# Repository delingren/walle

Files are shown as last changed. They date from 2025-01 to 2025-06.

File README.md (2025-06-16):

# Wall-E 3.0

* QR Code:

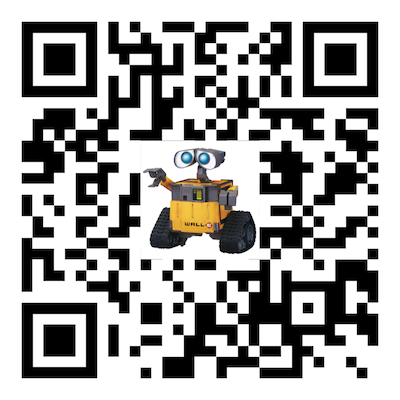
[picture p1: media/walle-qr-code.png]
qr_code
  

* Link: https://github.com/delingren/walle

## Intro

I bought this Wall-E toy made by Thinkway on eBay. Actually I bought a few, all partially broken. The toy is pretty primitive. It can make some basic moves. But the treads cannot be independently controlled. The arms can go up and down a little too, but not independently. The head can turn. The eyes can tilt a little bit. It only has one motor and it's smartly connected to all those parts with a gearbox to make them move in some ways. But in general, there isn't a high degree of maneuverability. It also has a speaker to make some sounds. When new, it came with an IR remote control. None of the units I bought still had it.

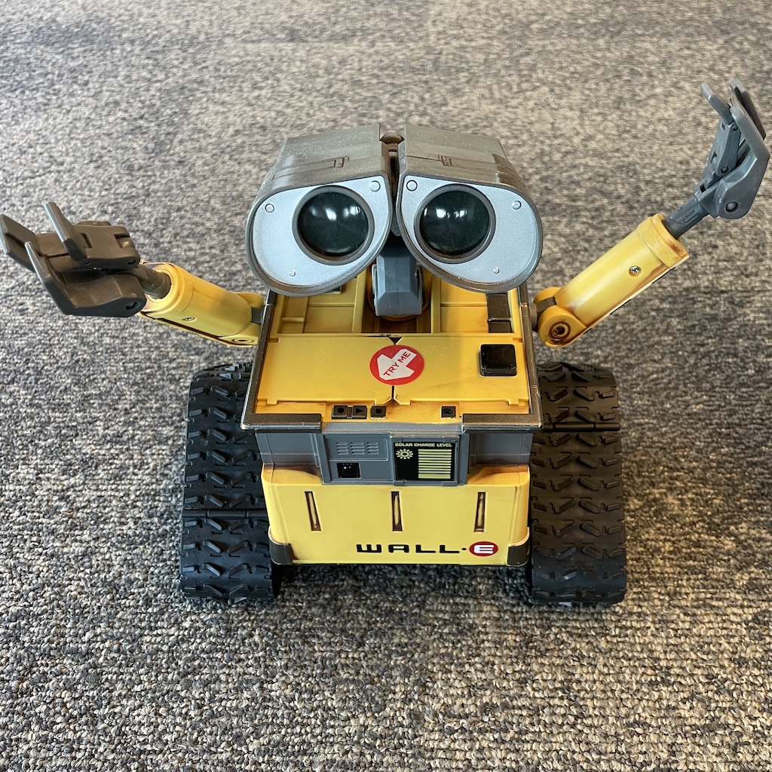
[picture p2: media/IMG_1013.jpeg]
wall-e


My plan is to control it with a microcontroller. The general idea is to gut the internals and replace them with my own parts. The objectives are as follows.

1. Treads can be controlled independently so that they can move forward and backward and at different speeds. This way, the robot can move forward, backward, turn while moving, and spin in place.
1. The arms can lift and lower independently. They only have one degree of freedom. It'd be too complicated to make them do more than that.
1. The head can turn left and right.
1. The eyes can light up. They each have a blue LED inside.
1. The eyebrows can raise and lower, which is done by tilting the eyes around the center.
1. It can play pre-recorded sounds.
1. It can be controlled with remote controls.

The general approach and necessary materials and tools:
1. All the mechanical parts will be 3d printed. I use Fusion 360 for 3d modeling and FlashForge Adventure 3 Lite for printing.
1. The central control unit will be a microcontroller.
1. I will be using Arduino framework to code the mcu.
1. Misc electronic components that will be described in details in this document. All can be found on Amazon or AliExpress.
1. Misc small screws, also found on Amazon or AliExpress.
1. Misc tools such as a soldering station and precision screw drivers and drills.

## Table of Content

The rest of the documentation is organized as follows.

* [Disassembly](disassembly.md)
* Prototyping
  - [Microcontroller](mcu.md)
  - [Controlling arms](arm.md)
  - [Rotating the head](head_rotation.md)
  - [Driving the treads](drivetrain.md)
  - [Driving the eye tilter](eyetilt.md)
  - [Audio](audio.md)
  - [Remote receiver](remote_receiver.md)
* [Remote Control](remote_control.md)
* [RC protocol](remote_protocol.md)
* [Integration](integration.md)
* [Firmware](firmware.md)
* Schematics
  - [Main unit](./schematics/main.svg)
  - [Remote control](./schematics/remote.svg)

* 3D models
  - [Fusion 360 file](./stls/walle_3.0.f3d)
  - [STL files](./stls/)

## Demo

Here is the demo video (on YouTube) of the final product, controlled by a Roku remote control and my custom remote control. It opens on youtube.

demo (https://youtu.be/jzXZmGbrTi8)

## Remote functions

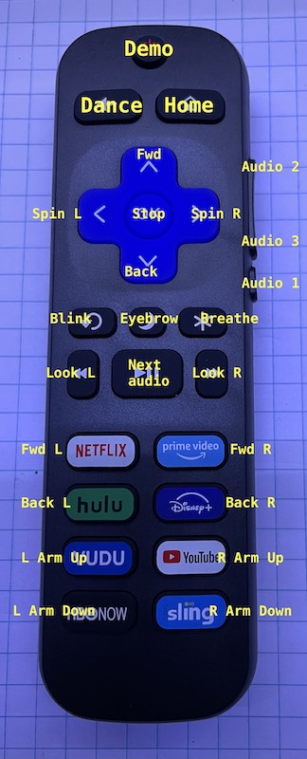
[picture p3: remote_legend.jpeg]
remote_legend


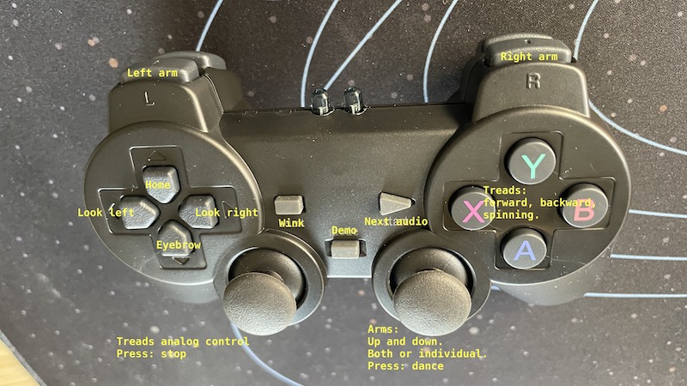
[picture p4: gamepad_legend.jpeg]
gamepad_legend


## Improvement goals over 2.0:
* Use a H-bridge that can provide more voltage hence more torque. In v2, I used an L293D H-bridge IC to drive the DC motors. It turned out it has a pretty high voltage drop. According to the datasheet, the typical motor output voltage is `Vcc - 2.6` and can be as low as `Vcc - 3.6`. I am going to use a MOSFET based H-bridge which would have a much lower voltage drop. I might need to increase the size of the prototype PCB and hence its mount.
* Utilize the "play" mode of the switch. The switch has an off position, and two on positions. One of them is marked as "play" mode. That position connects two additional wires. I can wire one of them to `GND` and another to a GPIO pin, so that I can read from the MCU, thus distinguish the play mode.
* Revise IR remote protocol for better reliability and faster response. In v2, I used a protocol that sends a 32 bit code for each event: button press or joystick coordinate change. The transmission takes 63ms, which means the fastest I can achieve is 15 frames per second. I decided to take a different approach and transmit the state of the gamepad in each frame with 40 bits. The frame rate is still low (actually even lower), but I can transmit the full state of the gamepad in each frame.
* Improve IR remote control for better range. In v2, I drive the IR LED with a GPIO pin, which does not provide enough power. So I'm planning to use a transistor to amplify the signal, and potentially use two LEDs (one wide beam, one normal beam). If the current burst is too much for the batteries to handle and causes the MCU to brown out, we may change the fuses on the Arduino Pro Mini to lower the BOD level.
* Make it possible to change the audio files. In v2, I uploaded the audio files to the audio module's internal flash and soldered it. So it's fixed to UART mode after booting, and the content cannot be 
* Fix the bug where the numbering of the audio files is messed up. Previously, I noticed that the numbering of the audio files did not align with the file names. It turned out that the order has nothing to do with the file names, but is rather dependent on the order of the files in the file system. See [this note](https://github.com/SnijderC/dyplayer?tab=readme-ov-file#important-files-do-not-play-in-order-of-named-sequence). What's the point of naming the files in the specific way then?! I'll try to upload the files individually, from a Windows box.

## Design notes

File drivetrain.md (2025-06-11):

# Driving motors with H-bridges

The main motors need to be able to rotate both directions and the speed needs to be controlled. So we'll use two H-bridges. In v2, I used an IC L293D that has two full H-bridges and can drive 600mA. However, once integrated, I found that the motors were not providing enough torque. I had to reduce the gear ratio and used two 75RPM DC motors. This resulted the tread moving more slowly than I wanted. I did a some trouble shooting and concluded that the two main reasons were the voltage drop on the H-bridge and lack of lubrication in the system. The second was easy to solve with some bike chain lube. For the former one, I decided to look for a different H-bridge IC based on MOSFET instead of BJT. So I came across [this post](https://dronebotworkshop.com/tb6612fng-h-bridge/) that introduces this TB6612FNG breakout board. It uses 6 GPIO pins rather than 4, 3 for each motor. Two pins control the direction and a third one controls the speed via PWM.

So I loaded a [sketch](./debug/motor_hbridge/) to test controlling the speed and direction of two motors. It tries different directions and speeds.

drive_train

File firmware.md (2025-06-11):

# Firmware

There are two independent parts. One for the main toy and one for the remote control. I'm using Arduino framework for both.

## Main

The firmware is relatively straight-forward. One thing worth mentioning is animation. When we receive a command, such as turning the head, we want the operation to be rather smooth. So, instead of setting the position immediately, we animate the transition to the target position. Animation is also needed to create breathing patterns in the eyes. This also applies to the speed of the motors so that they accelerate and decelerate smoothly. So I am defining an `Animatable` class and keep a list of ongoing animations at any moment.

There are at least these two orthogonal aspects to an animation.
1. Absolute value / relative value
1. Transition time / transition speed

So I have defined all these permutations, in addition to a constant animation (or in-animation?). All the transitions are linear. This should be enough for this simple application. Every time we execute `loop()`, i.e. in each frame, we update all the status of all animations.

1. For an ongoing animation, we calculate its transient value by interpolating using the start time, duration, initial value, and target value.
1. If an animation has reached its target value, we remove it from the list and enqueue the next animation.
1. When a new animation is enqueued, we calculate its target value if its value is specified in relative terms.

With the animation library, we can then easily choreograph sequences of moves and associate them with remote control buttons. Since we also have a play mode and a trial mode, we can also do different things based on the mode. I have defined a `trialMode` boolean in the sketch. I'm only using it for the startup moves so far.

### Libraries

Instead of relying on Arduino IDE's library manager, I enlisted DYPlayer and IRRemote libraries as submodules and froze them at the current version. So that it's more self contained and resistant to future breaking changes to these libraries. The Servo library, however, is part of RP2040 board SDK which uses PIO instead of PWM. There is no need to enlist it as a submodule, unless I also enlist the whole SDK, which is unnecessarily complicated.

After enlisting these two libraries, I linked all files in their `src` directories under my sketch's `src` directory. Arduino Framework link all source files under `src` directory. I don't know if there is a way to add a local library. But creating symbolic links is pretty straight-forward with the following bash commands.

```
for i in ../../third_party/Arduino-IRremote/src/* ; do; ln -s $i ; done
for i in ../../third_party/dyplayer/src/* ; do; ln -s $i ; done
```

## Remote Control

The remote control protocol is described in [its own chapter](./remote_protocol.md). The code implementing the sender side simply scans the state of all the controls and sends out a packet. Since the transmission rate is rather low (10 frame per second at most), we don't need to do any debouncing for the buttons. The only interesting bit is scanning the matrix. I'm scanning from column to row. All row pins are pulled up high by default. When we scan, we pull down the column row. If a key at the intersection of the col and row is pressed, it pulls down its row pin. So we can get the state of each button by scanning all the columns and reading all the rows.

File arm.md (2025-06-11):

# Controlling arms

I am going to use servos to control the rotation of the arms and the head. Mechanically, the arms pose a small challenge. I can't disassemble the arm assembly any further without risking damaging the plastic. So I can't get to the axles that the arms rotate around. But I came up with a reasonable solution using the existing mechanism, not requiring the servo shaft and the arm axles to be concentric.

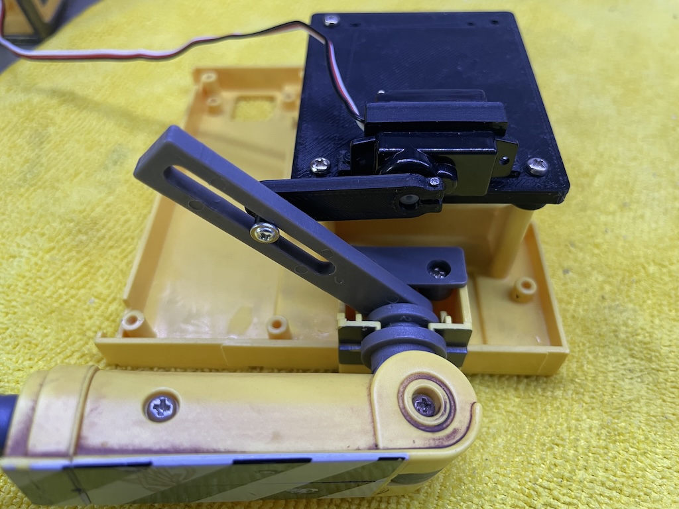
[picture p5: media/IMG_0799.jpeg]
arm_servo


I am using a 5g servo WK-P0050 that I bought from [Amazon](https://www.amazon.com/gp/product/B09TKLQ44L). It's not available there anymore but can be found on AliExpress and other sites.

The servo is fixed on the upper platform with a clamp. The crank is clamped to the servo shaft using an M1 x 5mm screw and a nut. The screw and nut are tiny! The STLs of these parts can be found in the [`stls`](./stls/) folder.

A servo normally rotates 180 degrees. But I don't necessarily need all that range. Its position is controlled with a PWM signal, whose duty cycle width determines the position. Pi Pico's servo library supports specifying the width in microseconds in addition to angles in degrees. So, I am going to map range `[0, 1]` to the minimum and maximum PWM widths, corresponding to the physical range I need for each servo. This way, my code only needs to specify a value between 0 and 1 and the servo will be set to the corresponding position. The details of the servo are abstracted away.

To find out the PWM width ranges, I wrote a [sketch](./debug/servo_calibrate/) which reads a number from the serial console and outputs it to the servo. This way, I can manually enter values to move the servo and find out the minimum and maximum values.

Next, I wrote a [sketch](./debug/servo_sweep/) to sweep the servo back and forth within the range.

sweep

Sweet! Now onto the servo for the head.

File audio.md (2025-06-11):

# Audio

## DFPlayer

I used a [DFPlayer](https://www.dfrobot.com/product-1121.html) in the first version and thought it was a bit expensive (~$20 at the time). But the price has come down quite a bit. AliExpress even has some clones that costs just a little over $1 a piece. It doesn't have internal flash. Instead, it reads from microSD cards. I have quite a few of microSD cards salvaged from all sorts of electronics found in e-waste bins.

So, let's see if it plays nicely with the RP2040-Zero. The board comes with an Arduino [library](https://github.com/DFRobot/DFRobotDFPlayerMini). The wiring is rather simple. You just need to provide it with power and connect it with a UART port, which I'm using `Serial1` on Pi Pico (pins 0 and 1 by default for Tx and Rx respectively), and connect the speaker to the output pins. There isn't much to it. Then I loaded a [sketch](./debug/dfplayer_loop/) to play all 10 audio files on the SD card in a loop. And voila, Wall-E can speak! A couple of caveats to mention:

1. For some reason, reading file count is not very reliable on this board. I think it's this particular board, since I didn't have any issues in the past. No big deal, I just need to hard code it.
1. The board takes 5V DC but I am going to power everything with 4xAA batteries and I hope to get away without using a regulator. It seems to be able to tolerate 6V. But it's safer to put a 1N1007 diode in serial to drop 0.7V.

## DY-SV17F

I also found an even cheaper alternative: DY-SV17F which has 4MB internal flash and a 5W amp. It has some [official documentation](https://github.com/smoluks/DY-SV17F) but no official Arduino library. I found a third party [library](https://github.com/SnijderC/dyplayer) and decided to give it a try with the following [sketch](./debug/dy_sv17f_loop/), similar to the previous one.

It seems to work fine. So I may go with this one for its low cost and simplicity, since it requires no SD card. A few things worth mentioning:

1. The datasheet states that it requires three 10K Ohm resistors to configure it as UART mode. However, in practice, shorting those pins works just fine.
1. It comes with a micro USB port for accessing its filesystem on the flash. It might be an isolated incident but when I copied files from a Mac, the file system was somehow corrupted. I later formatted it and copied the same files from a Windows box and everything was fine.
1. According to the datasheet, the file names need to be in the format of `ddddd.mp3` where `d` is a digit. 
1. Despite conforming to the file name convention, the numbering didn't seem to work in v2. Later I figured out that it actually goes by the order the files are copied, not the names. So I made sure to copy one file at a time and it worked fine.

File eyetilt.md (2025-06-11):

# Driving one-direction motors

The eye tilt is controlled with a single shaft rotating either direction. The shaft is directly connected to an N10 DC motor. There's no need for an H-bridge since we only need one direction. Instead, we need be able to turn it on and off with a MOSFET. We could use a PWM pin to control the speed but that's really unnecessary. We only need one speed.

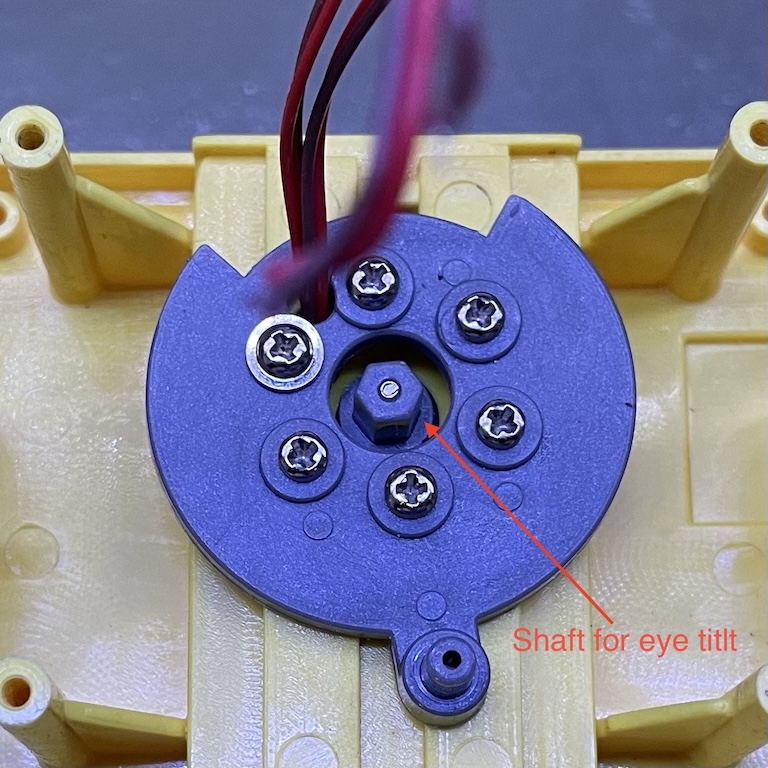
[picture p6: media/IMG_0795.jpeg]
eye tilt shaft


First I connected the motor directly to a 5V power supply and measured about 50 mA of current. So a 2N7000 MOSFET should be good enough to drive it. So I made a quick breadboard prototype and loaded a [sketch](./debug/motor_unidirectional/) to run the motor 3 seconds on and 1 second off repeatedly. It works perfectly.

eye tilt

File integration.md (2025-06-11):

# Integration

## Electronics

I am dividing the electronics into two parts. The lower part is mounted on the chassis near the drive train. It contains the MCU, the audio player, and the H-bridges. The upper part is basically a hub for everything related to the head, arms, IR remote, and the push button. The two parts are connected with a ribbon cable and Dupont connectors.

The power source is first fed to the switch. The switched power is then fed to both the upper and the lower parts. The switch is a three way one. In addition to on and off, there is also a "try me" mode. In that mode, two extra wires are connected. I didn't use it in v2. But here I am connecting one of them to `GND` and the other to a GPIO pin so that we can read the mode. So here's the finished switch, with one input and two outputs. The connectors are 2-pin JST RCYs. The female end can be directly plugged into standard 2.54mm Dupont male connectors. I had to enlarge the existing holes on the switch PCB using a small file. Otherwise it's rather trivial to cut existing wires and solder new ones. The following picture was taken before soldering wires for the mode switch.

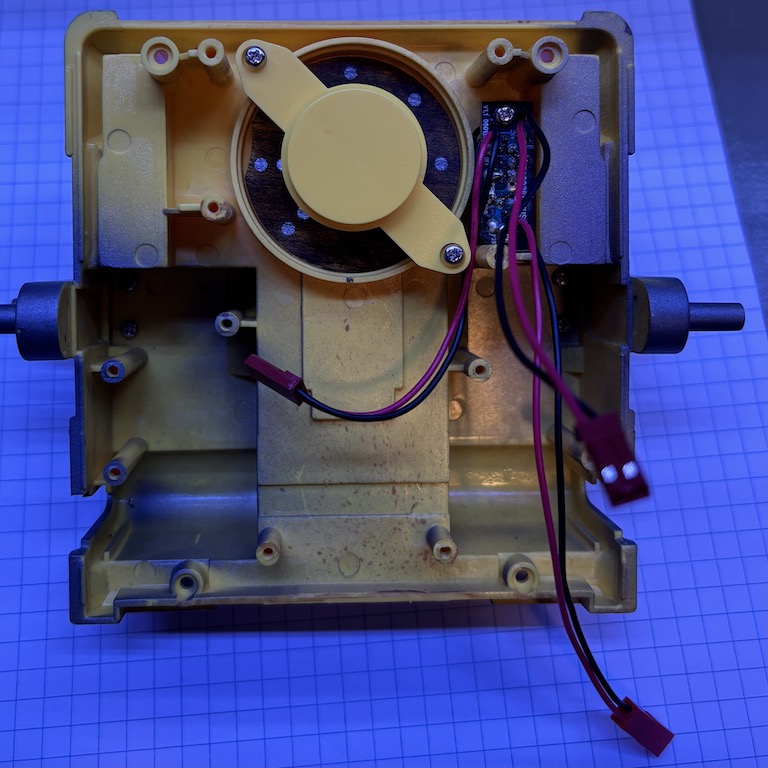
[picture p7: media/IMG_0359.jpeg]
switch


I soldered all electronic components onto a perf board. It has the following interfaces:

* Power source
* Mode switch
* Left and right motors
* Speaker
* Connectors for the upper part

To help with soldering, I first drew all the connections using [Acorn](https://flyingmeat.com/acorn/), a simple image editing tool running on macos, capable of layer editing.

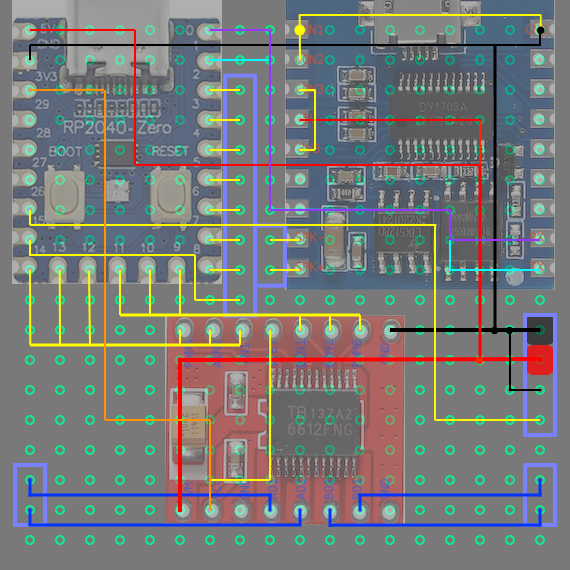
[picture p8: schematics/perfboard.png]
pcb_diagram


Here's the soldered perf board:

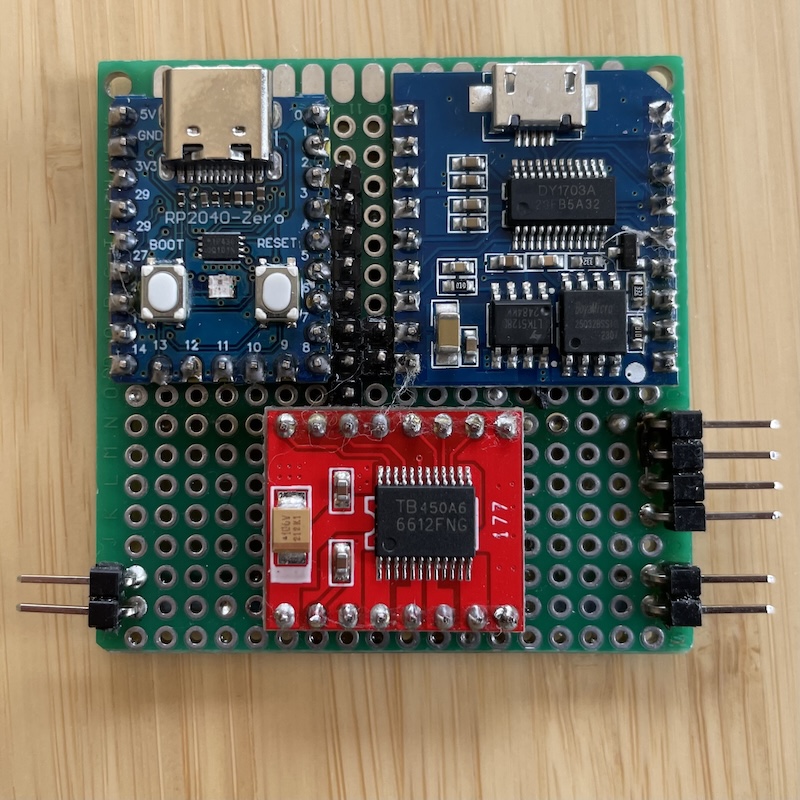
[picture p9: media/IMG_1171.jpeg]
lower_pcb


The PCB is then mounted to the chassis using a 3D printed mount.

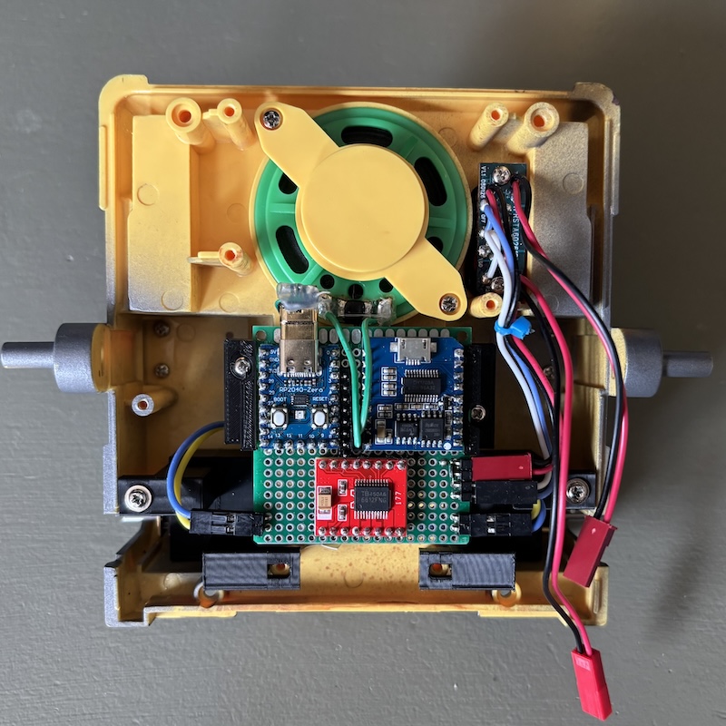
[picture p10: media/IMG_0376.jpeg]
mounted_pcb


Now the upper part. I want to have a neat interface between the upper part and the lower part for easy assembly. So I use a small PCB as a hub and plug everything in the lower part into its pin headers. The PCB has a power bus connected to the switched power source. Then I use a flat ribbon cable to connect all the logic signals. The two IR receivers' signals are combined on the PCB and fed to the MCU via one pin. The MOSFET for the eye tilter motor is also integrated to the PCB. Here are the connections.

1. Eye tilt motor - GPIO 2 
2. IR receiver, front - GPIO 3
3. Eye, right - GPIO 4
4. Eye, left - GPIO 5
5. Head - GPIO 6
6. Arm, left - GPIO 7
7. Arm, right - GPIO 8
8. Push button - GPIO 9
9. IR receiver, back - GPIO 3

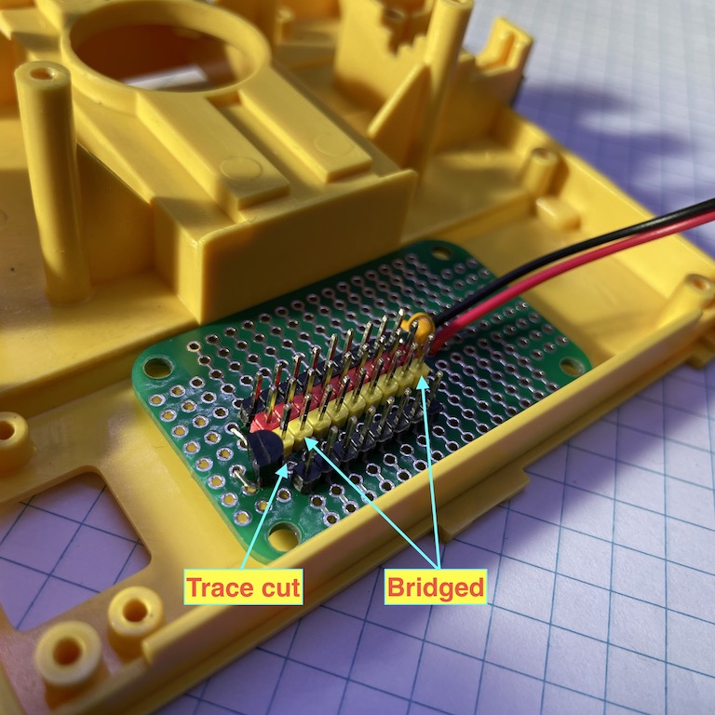
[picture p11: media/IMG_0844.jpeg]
upper_pcb


## Mechanics

For the main drive train, I am mounting the DC motors directly the to driving wheels, using 3d printed parts. The motors are connected to the outputs of the H-bridges. I was originally planning on using a couple of N20 5V 100rpm motors. But it turned out that they don't have enough torque. There is too much friction in the system (let's face it, none of the parts are precisely made and positioned, and there's no lubrication at all). So I ended up using two N30 6V 75rpm versions. They seemed to work fine.

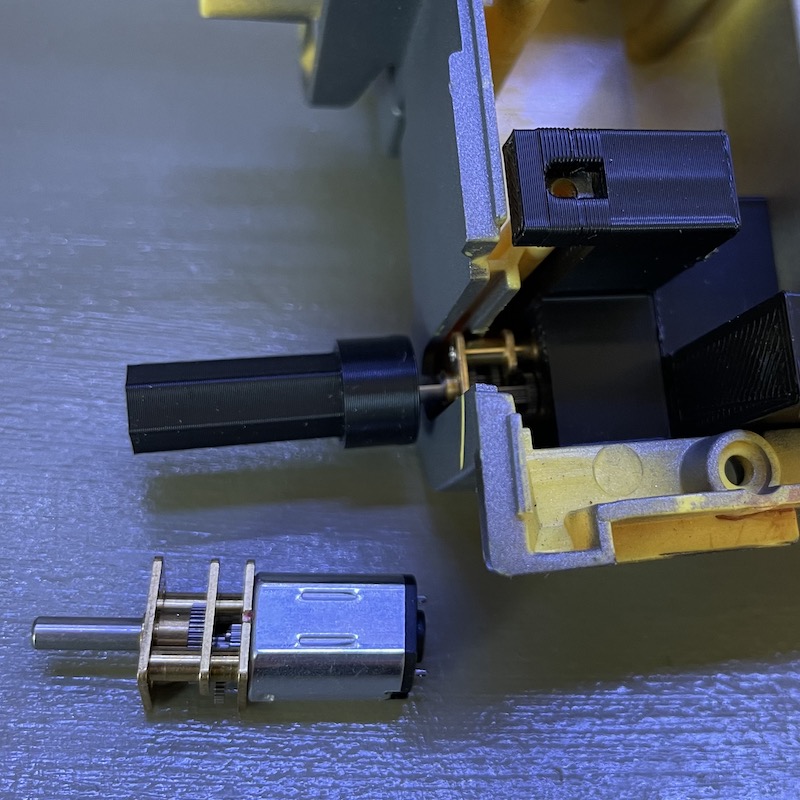
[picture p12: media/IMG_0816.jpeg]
drive_train


For turning the head and tilting the eyes, I already described the mechanism [here](./head_rotation.md) and [here](./motor.md). The servos for driving the arms are described [here](./arm.md). Altogether, I am mounting the three servos and the DC motor on an upper platform.

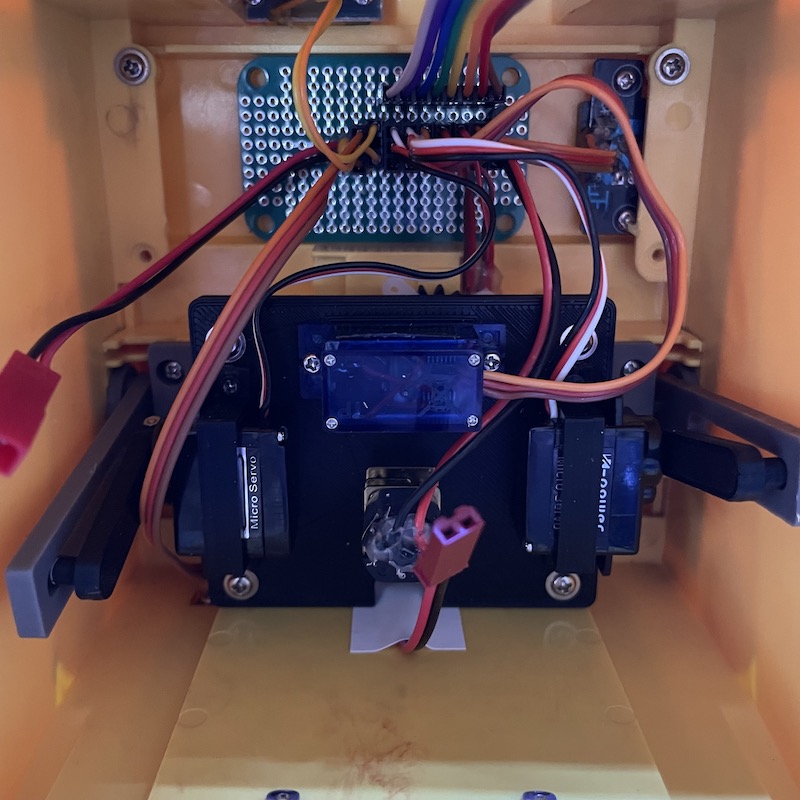
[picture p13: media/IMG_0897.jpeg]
servos


## Calibration and debugging

Before working on the final sketch, I am going through the following steps to make sure all parts are mechanically functioning as expected.

For the upper part:

1. Verify eye LEDs
1. Verify IR remote receiver
1. Verify eye tilter motor
1. Verify push button
1. Verify arm and head servos
1. Calibrate servos to determine their limits

upper

For the lower part:

1. Verify both DC motors can turn both directions and the speed can be controlled with PWM pins

lower

Before closing everything up, I am also exposing a USB-C port for uploading sketches and debugging through the serial port. To do this, I cut a hole at the bottom of the chassis, and mounted a panel-mount USB-C port (bought from AliExpress). Then soldered a male USB-C plug on it. Note that I am not connecting the V+ wire, to avoid accidental current backflow to the computer. So it needs to be powered by the batteries when uploading the sketch.

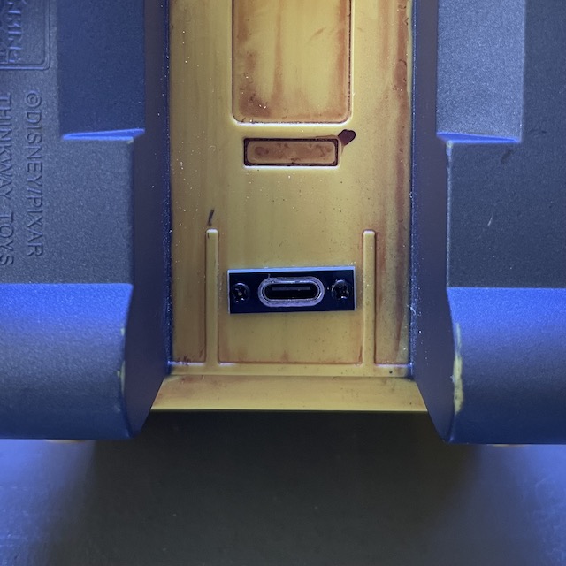
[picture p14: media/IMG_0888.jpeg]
bottom_usb


Now all the mechanical parts are in place and properly assembled. It's time to play with the firmware.

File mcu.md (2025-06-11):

# Microcontroller

We need to choose a microcontroller. I am not going to make a custom PCB for this project. Instead, I will use a dev board and a perf board. There are a few factors to consider.

1. There needs to be enough pins.
1. Dimension. We want the board to be compact.
1. Power. Ideally, I want to be able to power the board with 4 AA batteries, so that I don't need an extra 5V DC regulator.

Here's a tally of the minimum pin needs. These pins will be explained in detail in later sections.

* PWM output: 7 pins
  - Left tread H bridge (1)
  - Right tread H bridge (1)
  - Left eye LED
  - Right eye LED
  - Eye tilt motor

* Digital output: 4 pins
  - Left tread H bridge (2)
  - Right tread H bridge (2)

* Servos: 3 pins. Generally, libraries use PWM to control servos. Some may use PIO on Pi Pico.
  - Left arm servo
  - Right arm servo
  - Head servo

* Input: 2 pins
  - IR sensor
  - Push button

* UART for audio: 2 pins. Note that not all pins can be used for UART.
  - Rx
  - Tx

I have a few [RP2040-Zero dev boards](https://www.waveshare.com/rp2040-zero.htm) in my drawer. They are compatible with Raspberry Pi Pico but has a much smaller footprint.

* Dimensions: 18 x 23.5
* Regulator: ME6217 (LDO, 800mA, max input 6.5V)
* GPIOs: 20 via the header, all capable of PWM.
* UART: 2; UART0 defaults to GPIO0(Tx) and GPIO1(Rx).

It seems to fit the bill really well. So I'll be using it during the prototyping phase and see if it works for everything.

First off, let's verify that all the GPIO pins are PWM capable by using a simple [sketch](./debug/pwm/) to dim LEDs. Sure enough, all these 20 pins are able to fade the LED. This takes care of the eyes. These pins should be good for controlling motors and servos as well. But let's verify on a breadboard in a minute.

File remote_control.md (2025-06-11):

# Custom Remote Control

In addition to using an existing remote control, I also wanted to make my own remote control with joysticks. The biggest challenge is probably 3d printing the housing. So I am exploring the option of using an existing wireless PS2 control bought on AliExpress, gutting the inside and replacing it with a microcontroller and adding an IR LED.

To do that, there are a few things I need to figure out.

1. The joysticks. A PS2 controller has two of them. They are both 2-axis joysticks. I assume they are resistive (i.e. potentiometers) and I should be able to use an ADC pin to read the position of an axis.
1. The IR emitter. This should be relatively easy. The library I use on the receiver side is also capable of sending.
1. The microcontroller. The PS2 controller is powered by 2 AAA batteries, I want to be able to reuse the power source. So I need an mcu that can be powered at 3V. First thing that came to my mind is ATmega 328. I have a couple of them and they are 8MHz versions.

## Microcontroller
As mentioned before, I intend to use an 8MHz ATmega328 dev board (Arduino Pro Mini clone), which should be able to run at 3V comfortably. So I am going to prototype everything on that board. One small caveat about working with this board is that ATmega328 comes in two versions: 8Mhz and 16MHz. When programming with Arduino IDE or CLI, we need to choose the correct frequency. Otherwise, the code will still run, but the timing is all messed up. Anything that relies on the frequency will not work properly. E.g. the serial console or the IR transmitter.

## Range
In v2, one issue I encountered was that the range of the remote control was poor. It turned out that these IR LEDs are designed to endure very high peak current, up to a few hundred mA, which GPIO pins cannot provide. So in v3, I am using a BJT to amplify the signal. In addition, I am putting two LEDs in series, one regular (TSAL6200) and one wide beam version (TSAL6400).

To test the range, I devised an easy tester. On the [sender side](./debug/irrange_sender/), I repeatedly send the same code. On the [receiver side](./debug/irrange_receiver/), I check and verify the code repeatedly. If the code is not received within a timeframe, I light up a red LED. If the code is incorrect, I light up a yellow LED. Then I can walk around the room and test how far I can walk from the receiver and it still remains green.

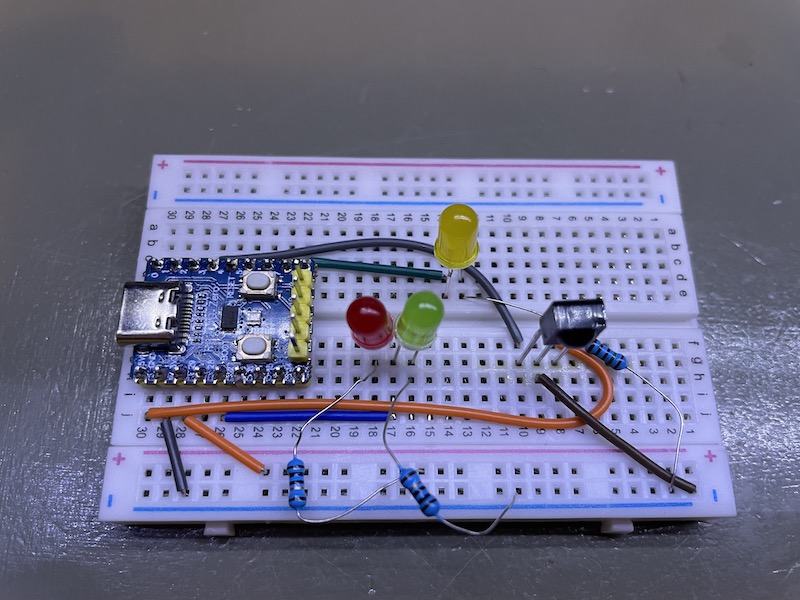
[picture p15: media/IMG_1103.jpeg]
range_tester


It turned out that with two LEDs in series, I can reach a range of at least 6-7 meters on my testing apparatus. In practice, since the IR receiver is behind a brown window, the reception is weakened and partially blocked. But it still works well within 3-4 meters. Not too bad.

### Power saving
The MCU itself can be powered by 1.8-5.5V DC. And since I'm using batteries, I don't need the regulator. Removing it will increase the battery life and eliminate the voltage drop. I connect the battery power directly to the `Vcc` pin. While I'm at it, I also removed the power indicator, the built-in LED, their resistors, and the reset button.

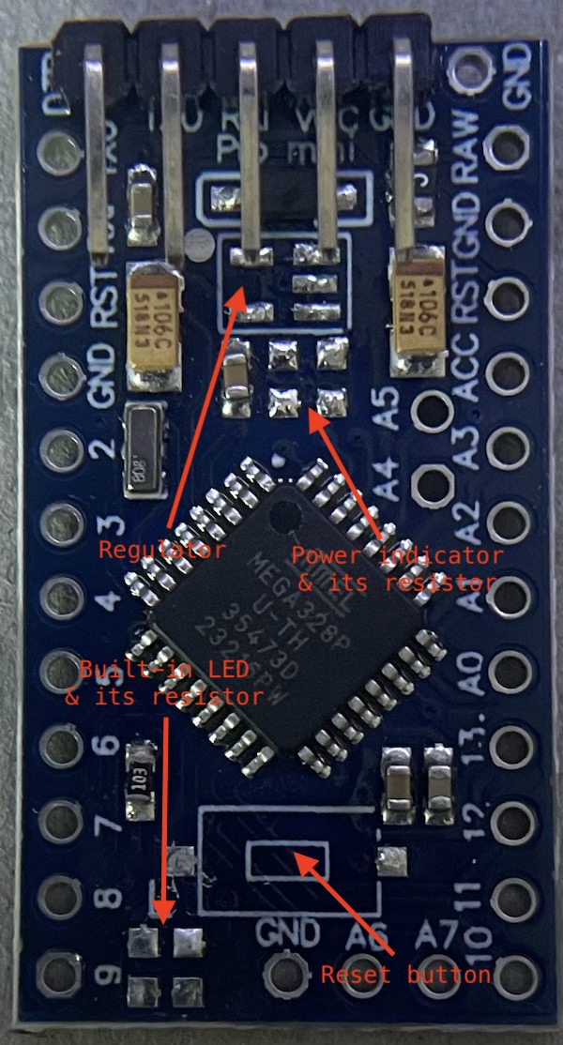
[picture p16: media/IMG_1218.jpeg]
arduino pro mini


## Controller Wiring
I got a couple of different wireless gamepad controllers from AliExpress and disassembled them. They both have tow major PCBs. PCB1, the main PCB, contains the battery box, the IC and various buttons. PCB2 contains two joysticks and a switch. Long story short, this particular one's main PCB has everything I need and needs minimum modification. However, it turned out its joysticks are digital, not analog. On the other hand, the other controller's joysticks are analog and the PCB has the same dimensions. So I created a Frankenstein controller from both of them. In the end, it worked fine. But it was a lot of soldering of thin wires under a magnifier and it was hard on the eye. Next time, I'll probably design a custom PCB and just reuse the shell.

PCB1 contains:
* Left thumb: `L`, `R`, `U`, `D`
* Right thumb: `A`, `B`, `X`, `Y`
* Left index finger: `L1` & `L2`
* Right index finger: `R1` & `R2`
* Middle section: `Select`, `Mode`, `Start`
* A main IC, a transmission IC, and some passive components

I have no use for the components except the two LEDs and their resistors. So let's heat up the PCB with a heat gun and remove them. I suspected all those buttons would be connected to the main IC in some way, forming a matrix. So I traced the PCB traces and determined the following connections.

| | col 1 | col 2 | col 3 | col 4 | col 5 | col 6 | col 7 | col 8 |
|---|---|---|---|---|---|---|---|---|
| **row 1** |  `R1` |  `R2` |  `L1` |  `L2` | `SEL` |`MODE` | |`START`|
| **row 2** |  `A`  |  `X`  |  `B`  |  `Y`  |  `D`  |  `U`  |  `R`  |  `L`  |

Then I marked the pads on the PCB. If two pads are connected with a trace, I use the same label. My hope is not have to cut any traces, which seems feasible here. The only small caveat is that the LEDs' resistors are somehow connected to pads 15 and 16, which is also columns 7 and 8. I don't know why and how it's multiplexed. So I de-soldered the resistors, taped the pads over using a piece of Kapton tape and put the resistors back in place with one pad soldered. Then I added a wire to connect the resistors it to pad 17 and `GND`. I plan to connect `LED1` it to `GPIO13`, the built-in LED pin, and remove the built-in LED on the dev board. I am going to light it up when sending signals. The other LED is the power indicator. Its anode is connected to `BAT+`. So I just connected its resistor to `GND` so that when `GND` is connected to the `BAT-` by the switch, the LED will light up.

And the pins for the rows and columns for the button matrix and the GPIO pin I intend to use:  
```
row 1: pad 06  (GPIO11)
row 2: pad 07  (GPIO12)
col 1: pad 04  (GPIO02)
col 2: pad 09  (GPIO03)
col 3: pad 10  (GPIO04)
col 4: pad 11  (GPIO05)
col 5: pad 13  (GPIO06)
col 6: pad 14  (GPIO07)
col 7: pad 15  (GPIO08)
col 8: pad 16  (GPIO09)
```

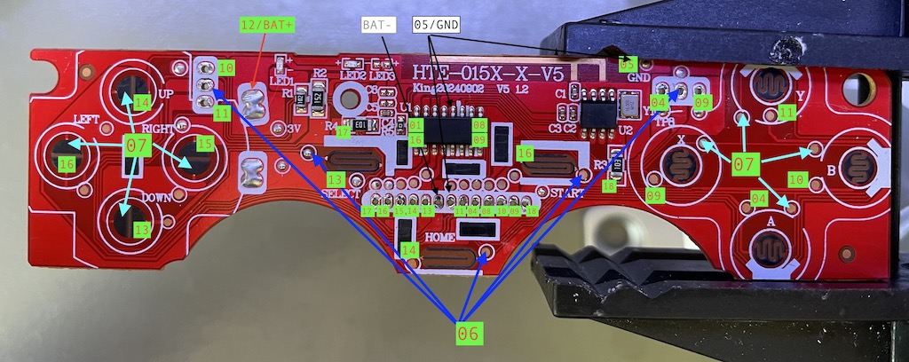
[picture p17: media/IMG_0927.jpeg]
pcb1


We will need these outgoing wires: 
* to PCB2: `BAT-`, `GND`
* to MCU: `BAT+`, `GND`, `Rows 1-2`, `Cols 1-8`, `LED1`

I shorted pads 7 and 8, pads 18 and 6, pad 17 and LED1. This way, all connections except `BAT+` can be made from the pads with holes in the middle.

PCB2 contains:
* Joystick 1, with axes `X1`, `Y1`, and button `J1`
* Joystick 2, with axes `X2`, `Y2`, and button `J2`
* A sliding switch `SW`

When turned on, the switch shorts `BAT-` to `GND`. The two buttons short their pins to `GND` when pressed. The joysticks are analog. Each axis is a potentiometer. It has a high and a low inputs. The output is the wiper. I'll short the low to `GND` and connect the high to  `GPIO A5`. I can then pull the pin high and read the wiper pins as analog pins to determine the position of the axis.

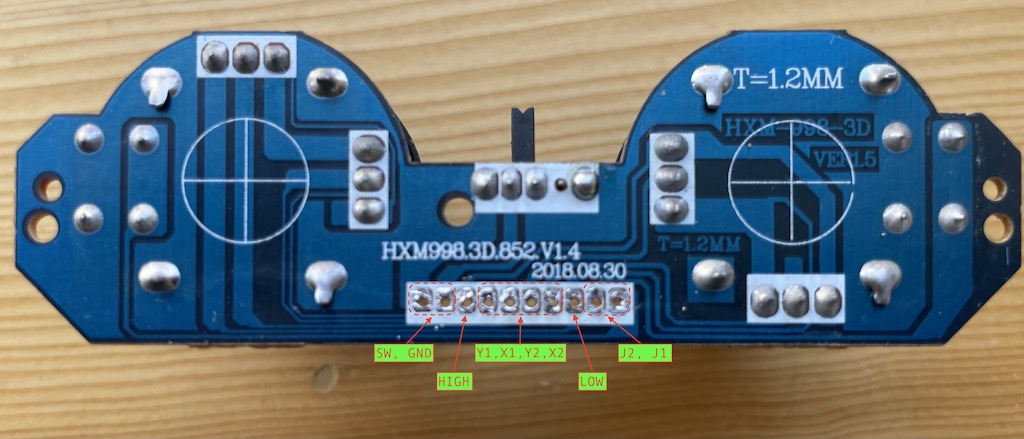
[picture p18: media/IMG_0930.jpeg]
pcb2


Here's the plan for connections:
* Short `LOW` with `GND`
* Connect `SW` to `BAT-` from PCB1
* Connect `GND` to `GND` from PCB1, which ultimately connects to `GND` of the MCU

This way, when the switch is turned on, `BAT-` is connected to `GND` of both PCBs and the MCU. 

Outgoing wires:
* to PCB1: `BAT-`, `GND`
* to MCU: `HIGH`, `X1`, `Y1`, `X2`, `Y2`, `J1`, `J2`

For the analog joysticks, we feed a high to `HIGH`, and read the positions from `X1`, `Y1`, `X2`, `Y2`. I could connect `HIGH` to `Vcc`. But I want to pull it high only when I'm reading the values. This will save a little battery, at the cost of using an extra pin. Now to tally all the GPIO pin usage, we need to use 17 input pins, 4 of which need to be able to analog. Note that `A6` and `A7` are analog input only for Pro Mini. So I'll use them for a joystick. Pin `13` is the built-in LED. I could remove the LED and reclaim the pin. But I might find a use for it later. So I'm saving pin `13`. We also need one digital output pin to drive the IR LED. That's 18 GPIO pins in total. The dev board I have, basically a clone of Arduino Pro Mini, has just enough.

PCB1 ↔ MCU:
* `BAT+` ↔ `Vcc`
* `GND` ↔ `GND`
* `Rows 1-2` ↔ `11`, `12`
* `Cols 1-8` ↔ `2` - `9`

PCB2 ↔ MCU:
* `HIGH`: `A5`
* `X1`, `Y1`, `X2`, `Y2` ↔ `A2`, `A3`, `A6`, `A7`
* `J1`, `J2` ↔ `A0`, `A1`

And,
* IR LED: `10`.

After some soldering and hot gluing, here are the PCBs and the dev board all connected.
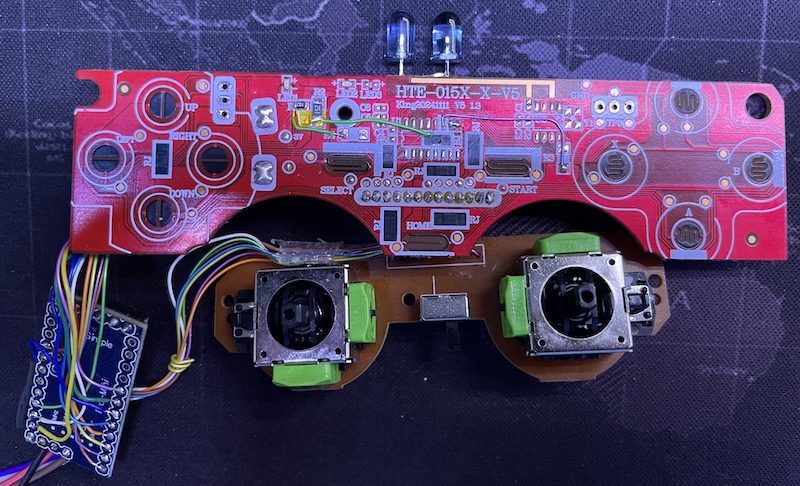
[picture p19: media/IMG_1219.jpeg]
soldered


And after some drilling and cutting, I've placed the IR LED on the shell, with the resistor soldered to it and `BAT+`.
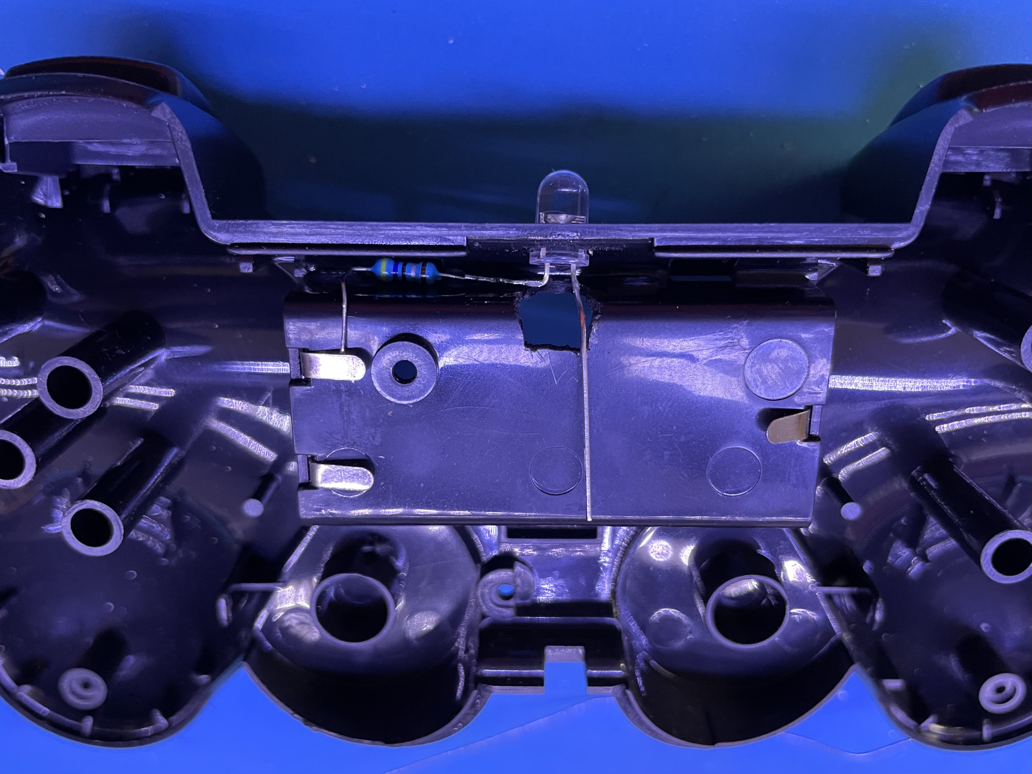
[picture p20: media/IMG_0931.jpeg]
shell


And voila! We have a custom remote control.

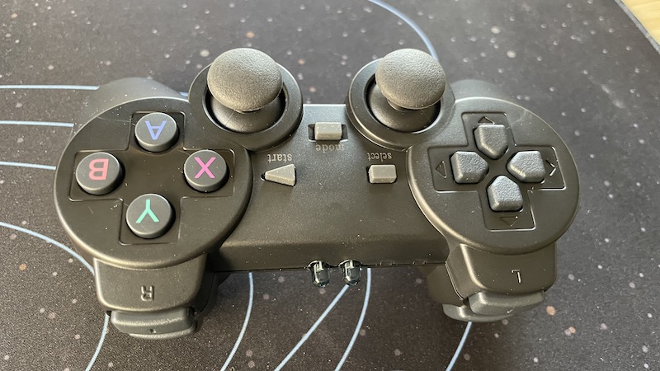
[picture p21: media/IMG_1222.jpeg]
finished


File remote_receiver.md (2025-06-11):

# IR Remote Receiver

The original toy came with a remote control but none of mine had it when I bought them. Not that I really want to use it. Instead, I want to be able to use an existing remote control. In addition, I want to make my own. Wall-E has two IR sensors, one on the shoulder and one on the back. I can either reuse them if they work or replace them with my own if needed.

First order of business is to verify that the sensors responds to my remote control. I have collected some remote controls from e-waste bins in the past. It's time to put them to good use. You probably have figured out by now that dumpster diving is one of my hobbies. Different manufacturers have different IR remote protocols. Many are either publicly available or has been reverse engineered. Here's a very [comprehensive tutorial](https://dronebotworkshop.com/ir-remotes) on this topic. To decode the signals, I am going to use this [Arduino-IRremote library](https://github.com/Arduino-IRremote/Arduino-IRremote). There are some other libraries available for Arduino.

First, I wired up a receiver and checked the waveform with an oscilloscope.

oscilloscope

Next, I loaded a simple [sketch](./debug/irreceiver_print/) to print out the raw data. I'm getting something like this on the serial console:

```
Protocol: 10 Raw code: 3759747205
Protocol: 10 Raw Code: 0
```

The particular remote I want to use is a Roku remote. It seems to use NEC and NEC2 protocols. All repeats are NEC2 and all initial presses are NEC. I don't need or want repeats. So I'll just decode NEC (8). Here's the list of the codes for all the buttons, which will be used in the decoding logic.

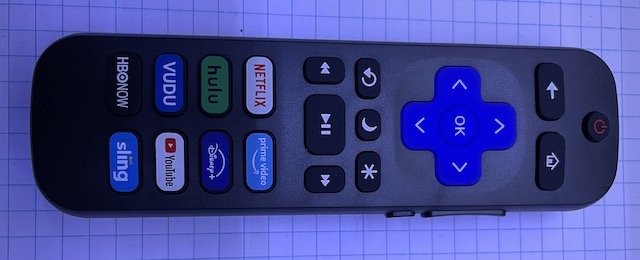
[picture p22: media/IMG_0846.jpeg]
remote


* Power: 3893872618
* Back: 2573649898
* Home: 4228106218
* Up: 3860449258
* Left: 3776890858
* OK: 3576350698
* Right: 3526215658
* Down: 3425945578
* Repeat: 2272839658
* Sleep: 2640496618
* Star: 2657208298
* Rewind: 3409233898
* Pause: 3008153578
* F. Fwd: 2857748458
* Netflix: 2907883498
* Amazon: 3024865258
* Hulu: 2991441898
* Disney: 4077701098
* Vudu: 4144547818
* YouTube: 2841036778
* HBO: 2974730218
* Sling: 4177971178
* Vol Up: 4027566058
* Vol Down: 4010854378
* Mute: 3743467498

A couple of notes:
* It looks like the receivers have no problem with 6V DC. So I am going to connect them directly to the power source.
* Putting two receivers in parallel doesn't seem to cause any problems. So that's what I am going to do.

I also want to be able to make my own joystick IR remote control. To do that, I can either devise my own protocol, since I have full control on both sides, or piggyback on an existing one, as long as it's capable of encoding all the info I need. The IR library I use is capable of both decoding and encoding.

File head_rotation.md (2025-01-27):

# Rotating the head

Since the head assembly is heavy, I am going to use a stronger 9g servo SG90, a staple servo that comes with any Arduino kit. I am replacing the original plate with a 3d printed gear with mounting holes matching the original holes on the plate. The original plate also has an opening whose either end would hit a limiter when the maximum range is hit. So I have removed some teeth from a full gear to achieve the same function.

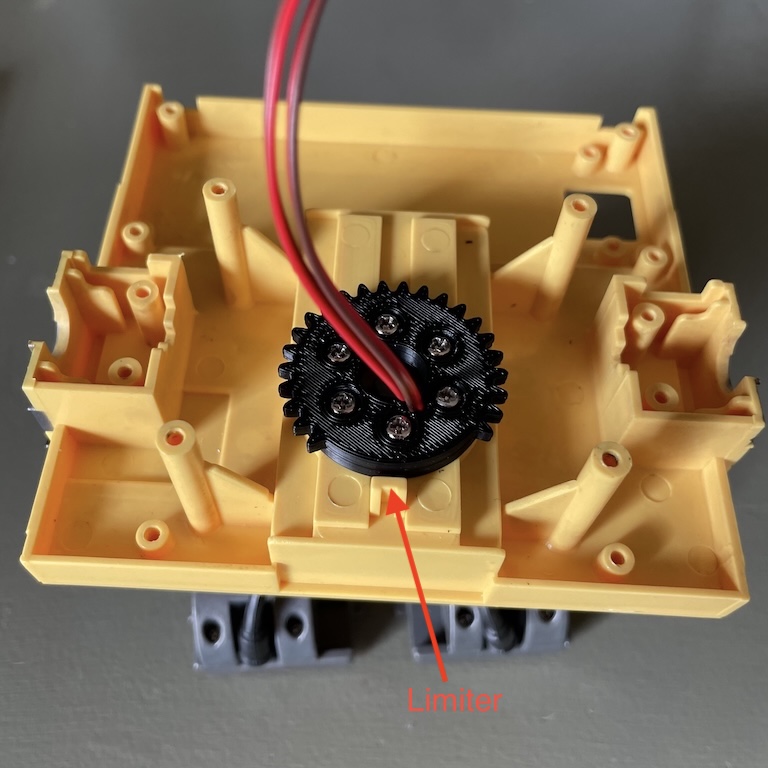
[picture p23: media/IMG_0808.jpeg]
head_driving_gear


Then I attach a 3d printed driving gear to the servo's arm.

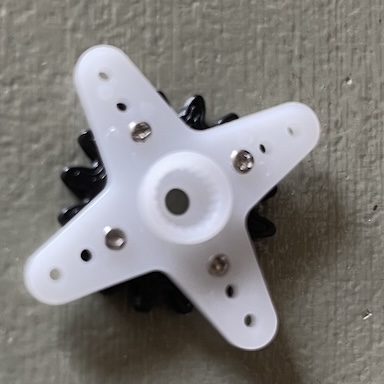
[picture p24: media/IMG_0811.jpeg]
driving_gear


The driving and driven gears are then meshed together.

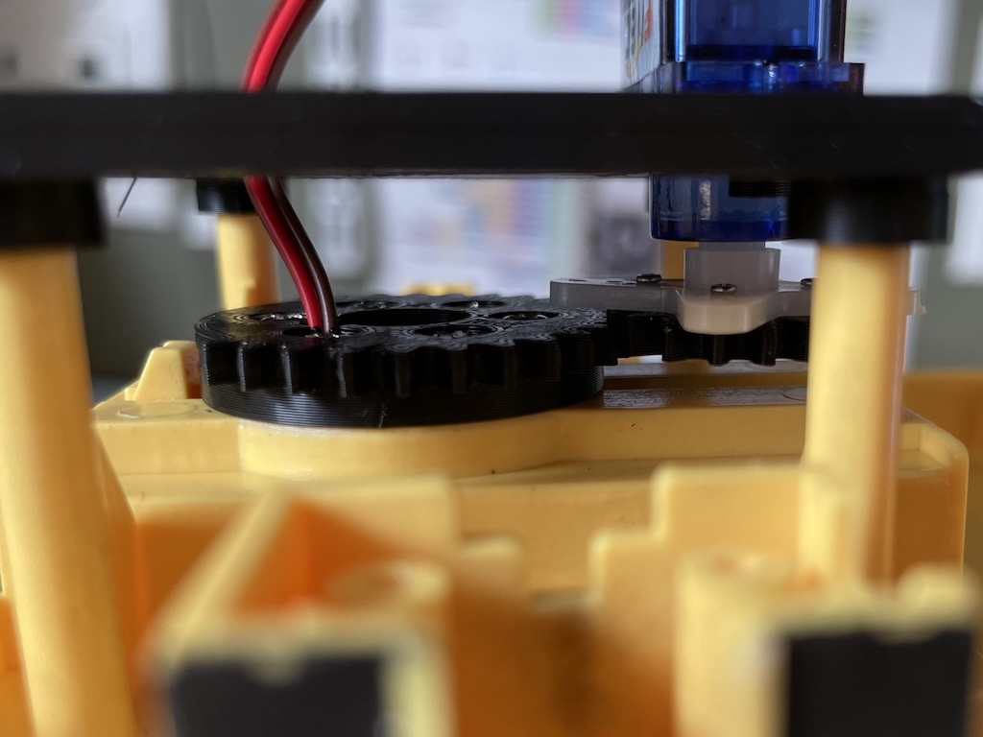
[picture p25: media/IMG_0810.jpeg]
gears_meshed


A note on generating the gears: I used the SpurGear add-in in Fusion 360 to generate them and manually customized them. The driving gear has 16 teeth and the the driven gear had 32, 9 of which were removed. The module is 1. I.e. the pitch diameters are 16mm and 32mm for both gears respectively. The backlash is 0.2mm.

Similar to the servos for the arms, I calibrated the range of motion of the servo and tested the sweeping motion of the servo.

head rotation

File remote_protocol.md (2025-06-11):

# Remote Control Protocol

## Control Protocol

In v2, I sent one event in one frame. An event is either a button press or joystick position change. This was a little inefficient due to the overhead to payload ratio of the transmission, which is very slow. So I decided to improve it by sending the state of the whole remote control in each frame, in 48 bits. To send more than 32 bits, I am using the following function call.

```
  // Protocol: 2 Raw Code: 0x0000BA9876543210
  uint8_t buffer[6] = {0x10, 0x32, 0x54, 0x76, 0x98, 0xBA};
  IrSender.sendPulseDistanceWidthFromArray(
    &NECProtocolConstants, 
    (IRRawDataType*)buffer, 
    8 * sizeof(buffer)/sizeof(buffer[0]), 
    0);
```

which is recognized as protocol 2 on the receiver side.

I noticed that the hobby level joysticks are not very accurate. In v1 and v2, I used 16 bits (8 each axis) for each pair of joystick coordinates. It turned out to be a big overkill. A resolution of 4 bits per axis is good enough. So I decided to use just one byte for each coordinate. Each coordinate takes a value of `[-7,7]` where `0` is the neutral position. To make things simple, I use 4 bits signed magnitude encoding to represent each coordinate. There are two reasons I use this subpar encoding, which has two representations of `0`:

1. I need an odd number of codes for symmetry. A two's complement encoding gives me `[-8,7]`. I waste a code anyway.
1. For some reason, the IR transmission doesn't work well with all zero bits. So I am using `b1000` to represent zero to avoid all zeros. I call that a happy incident.

## Code Format and Strategy
The following is the code format I use.
* Bits 47-40: xor of other 5 bytes, for error detection purpose. 
* Bits 39-16: bitmap representing button states. 0 for released and 1 for pressed.
* Bits 15-0: coordinates of two joystick.

Since the error rate is rather high, especially at the edge of the range limit, I decide to use an error detection byte so that the receiver can discard bad transmissions. Also due to lack of reliability of IR transmission, I need to repeat packets even if the state has not changed on the gamepad. But I also don't want to repeatedly transmit packets indefinitely when the gamepad is just idling. So I implemented an exponential back off strategy. When a repeat packet is sent, the interval before the next one is sent is increased by 1.5x. This way, when the gamepad stops changing, we'll send multiple repeats in short succession. But it'll slow down exponentially quickly.

## Translate Joystick Positions into Motor Control
Wall-E's movements are controlled by two treads, just like a tank or a bulldozer. The left and right treads can move independently. And I want to use a joystick to control its movements. Since a 2-axis joystick has 2 degrees of freedom, just like the treads, it should be possible to map the joystick positions to the tread movements precisely. And I want the mapping to be intuitive as well. It turned out that this isn't super trivial. So I am going to elaborate a little in this section.

Let's denotes the movements of the two treads first. They can move forward or backwards. Let's use 1 to denote a full speed forward move, -1 for a full speed backward move, and 0 for no movements. So, for Wall-E to move forward full speed, we need a (1,1); a full speed backward movement can be achieved by a (-1,-1). To spin in place left, we need a (-1,-1); to make a left turn pivoting on the left tread, we need a (0,1), etc etc.

Now consider the movements of the joystick. When the joystick is in the neutral position, there should be no movements. We want the control to be intuitive. So, pushing the joystick forward and backward along the Y-axis should make Wall-E to move along a straight line and the direction and speed are dependent on the joystick's position relative to the neutral position. Similarly, when the joystick moves along the X-axis, we should be spinning in place. When the joystick is in the upper-left corner, we should be making a left turn pivoting on the left tread. And so on and so forth.

Now, we can plot the nine key positions and the tread values. And we can draw arrows to represent the joystick movements from one position to another and the trends of the tread values along the way. And we will represent the position of the joystick with a normalized 2-dimensional coordinate. `(-1,1)*(-1,1)`.

```
            l-               l=
 (0,1)    ←────    (1,1)    ────→    (1,0)
            r=               r-
    ↑                ↑                 ↑
  l+│r=            l+│r+             l=│r+
    │                │                 │    
            l-               l+
(-1,1)    ←────    (0,0)    ────→    (1,-1)
            r+               r-
    │                │                 │
  l=│r-            l-│r-             l-│r=    
    ↓                ↓                 ↓
            l=               l+
(-1,0)    ←────   (-1,-1)   ────→    (0,-1)
            r+               r=
```

Then we can interpolate all the positions in between. Ideally, the range of motion of the joystick would be a circle. But a square will also do. The logic is going to be slightly more complicated. The following formula satisfies all the key positions and tread lines.

```
if (sign(x) == sign(y)) {
  l = sign(y)*max(|x|,|y|);
  r = sign(y)*(|y|-|x|);
} else {
  r = sign(y)*max(|x|,|y|);
  l = sign(y)*(|y|-|x|);
}
```

## Control Arms with a Joystick
I want to use the second joystick to control the arms' movements. Since the arms have two degrees of freedom between them, and the joystick has two axes, we should be able to do that. The problem is to find an intuitive way. Here are my goals:

* Forward/backward: raise or lower both arms
* Front left/back left: raise or lower left arm only
* Front right/back right: raise or lower right arm only

The remote control sends the raw positions of the joystick, just like the one that controls the treads. On the receiver (Wall-E) end, here's the logic.

* Determine if the joystick is to the left or right or in the middle, using the offset of the X axis.
* Raise or lower one or both arms depending on the previous result.
* The amount to raise or lower is determined by the offset of the Y axis.

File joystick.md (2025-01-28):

# Joystick Movements

Wall-E's movements are controlled by two treads, just like a tank or a bulldozer. The left and right treads can move independently. And I want to use a joystick to control its movements. Since a 2-axle joystick has 2 degrees of freedom, just like the treads, it should be possible to map the joystick positions to the tread movements precisely. And I want the mapping to be intuitive as well. It turned out that this isn't super trivial. So I am going to elaborate a little in this section.

Let's denotes the movements of the two treads first. They can move forward or backwards. Let's use 1 to denote a full speed forward move, -1 for a full speed backward move, and 0 for no movements. So, for Wall-E to move forward full speed, we need a (1,1); a full speed backward movement can be achieved by a (-1,-1). To spin in place left, we need a (-1,-1); to make a left turn pivoting on the left tread, we need a (0,1), etc etc.

Now consider the movements of the joystick. When the joystick is in the neutral position, there should be no movements. We want the control to be intuitive. So, pushing the joystck forward and backward along the Y-axle should make Wall-E to move along a straight line and the direction and speed are dependent on the joystick's position relative to the neaural position. Similarly, when the joystick moves along the X-axle, we should be spinning in place. When the joystick is in the upper-left corner, we should be making a left turn pivoting on the left tread. And so on and so forth.

Now, we can plot the nine key positions and the tread values. And we can draw arrows to represent the joystick movements from one position to another and the trends of the tread values along the way. And we will represent the position of the joystick with a normalized 2-dimensional coordiate. `(-1,1)*(-1,1)`.

```
            l-               l=
 (0,1)    ←────    (1,1)    ────→    (1,0)
            r=               r-
    ↑                ↑                 ↑
  l+│r=            l+│r+             l=│r+
    │                │                 │    
            l-               l+
(-1,1)    ←────    (0,0)    ────→    (1,-1)
            r+               r-
    │                │                 │
  l=│r-            l-│r-             l-│r=    
    ↓                ↓                 ↓
            l=               l+
(-1,0)    ←────   (-1,-1)   ────→    (0,-1)
            r+               r=
```

Then we can extrapolate all the positions in between. Ideally, the range of motion of the joystick would be a circle. But a square will also do. The logic is going to be slightly more complicated. The following formula satisfies all the key positions and tread lines.

```
if (sign(x) == sign(y)) {
  l = sign(y)*max(|x|,|y|);
  r = sign(y)*(|y|-|x|);
} else {
  r = sign(y)*max(|x|,|y|);
  l = sign(y)*(|y|-|x|);
}
```

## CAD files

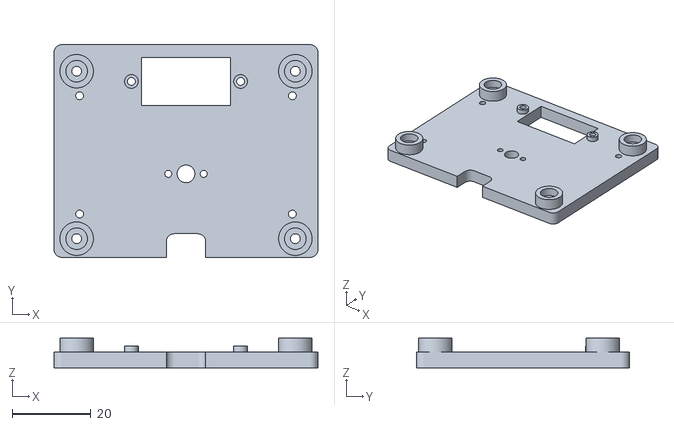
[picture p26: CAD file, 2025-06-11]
stls/upper_platform_1_body.stl
67.0 x 54.0 x 7.50

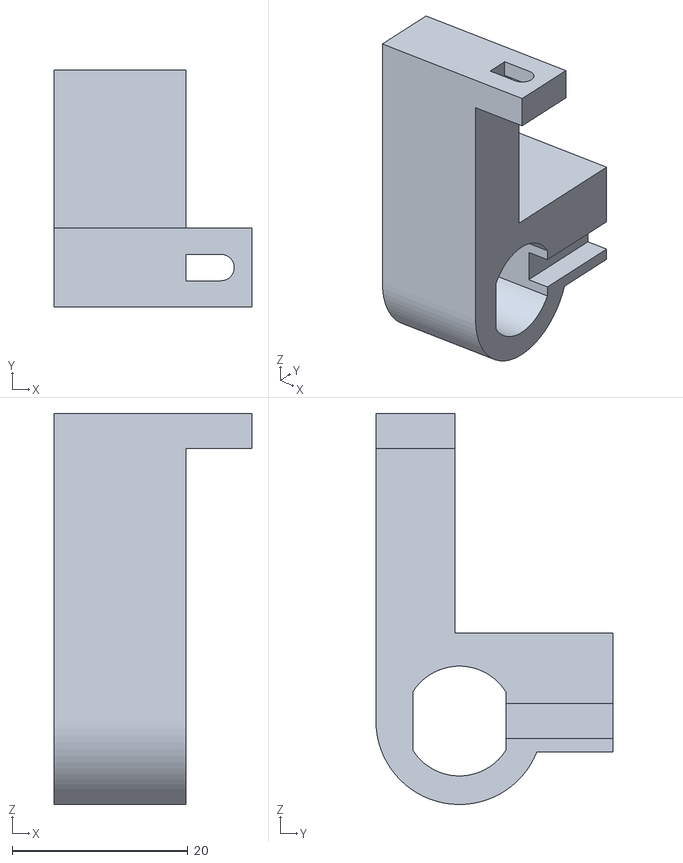
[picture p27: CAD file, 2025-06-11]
stls/drive_train_1_mount_l_i_1_body.stl
22.5 x 27.0 x 44.5

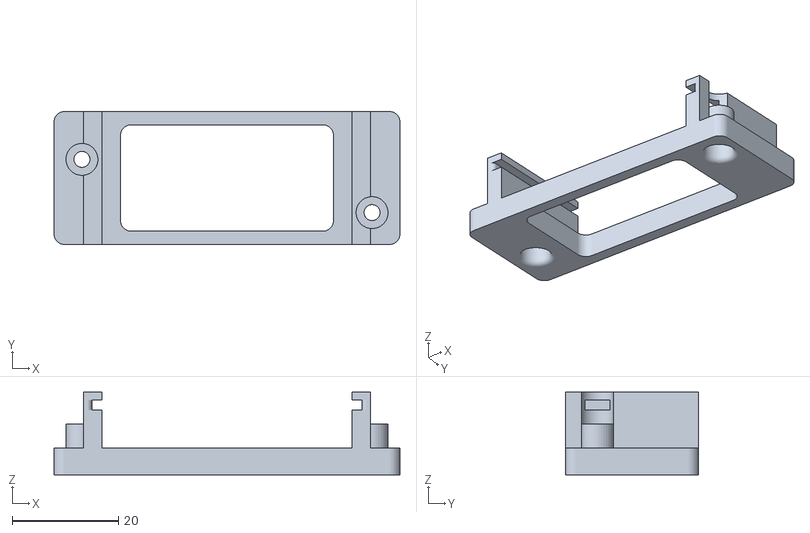
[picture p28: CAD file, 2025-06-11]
stls/pcb_platform_1_body.stl
65.0 x 25.0 x 15.5

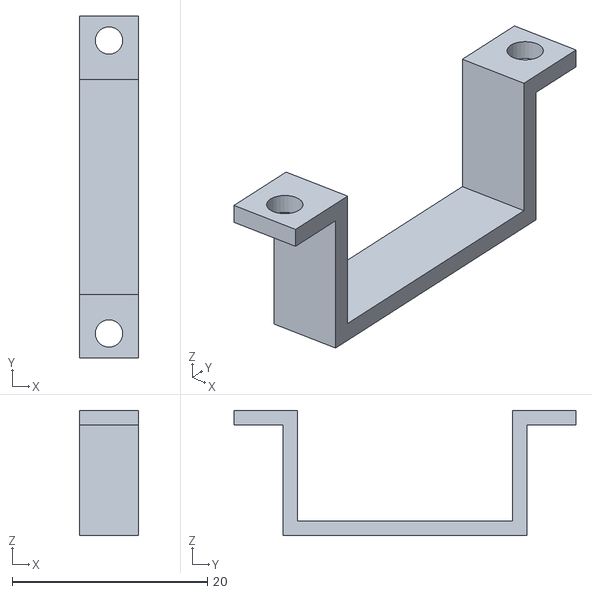
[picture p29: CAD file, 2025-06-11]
stls/arms_1_clamps_1_l.stl
6.00 x 35.0 x 12.8

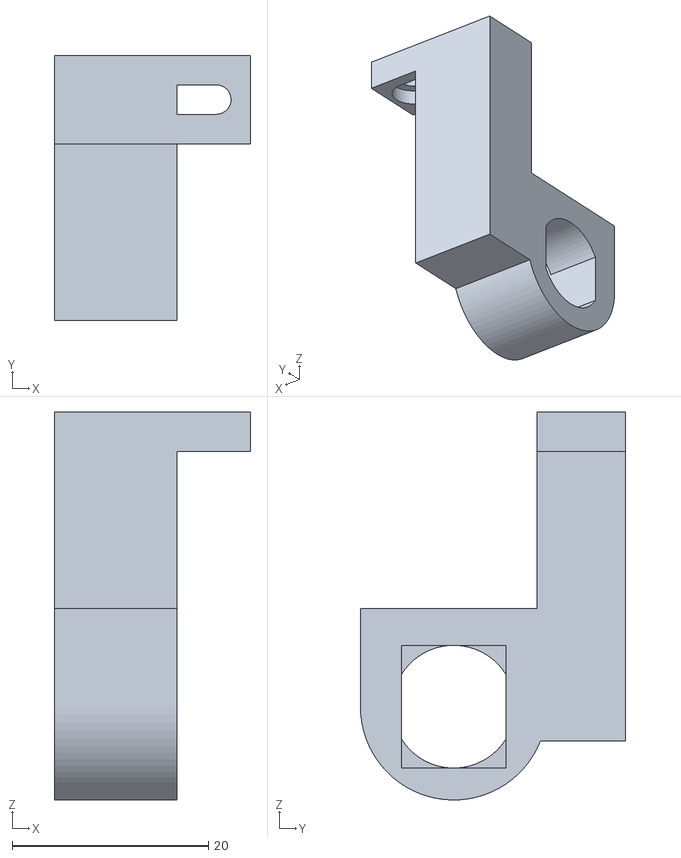
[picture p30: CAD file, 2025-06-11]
stls/drive_train_1_mount_r_o_1_body.stl
20.0 x 27.0 x 39.5

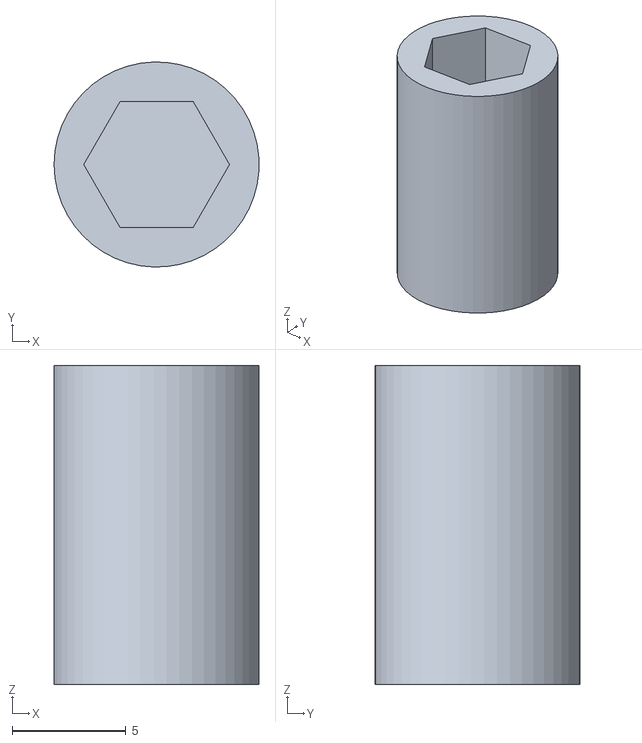
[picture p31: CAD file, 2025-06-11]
stls/head_1_eye_tilter_1_body.stl
8.99 x 9.00 x 14.0

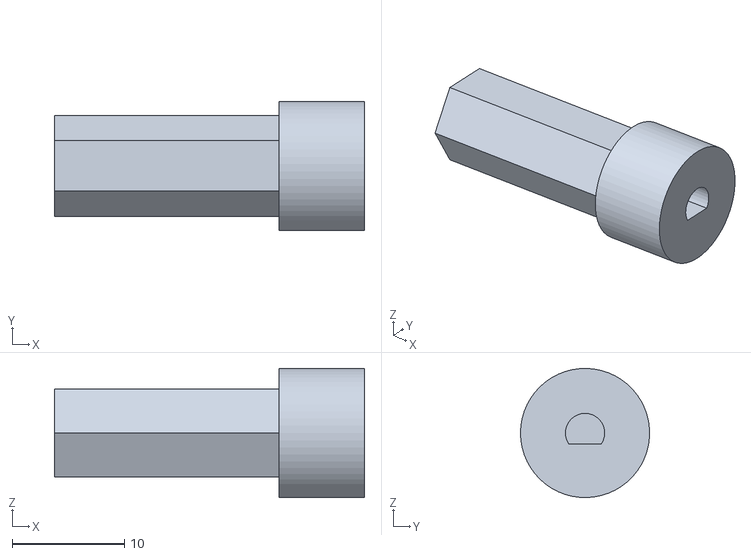
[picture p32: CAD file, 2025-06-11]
stls/drive_train_1_axles_1_l.stl
27.6 x 11.5 x 11.5

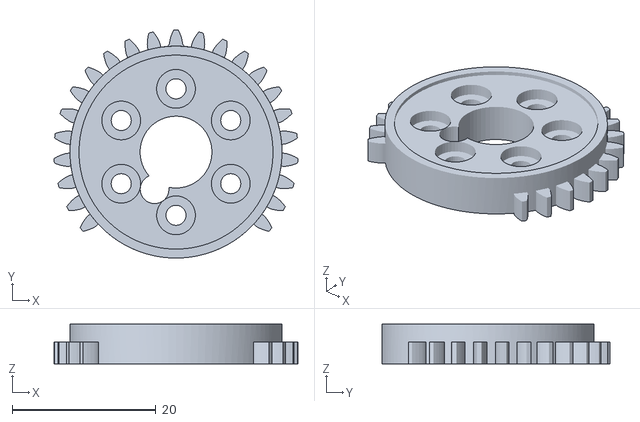
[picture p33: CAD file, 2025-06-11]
stls/head_1_driven_gear_1_body.stl
34.0 x 31.7 x 5.50

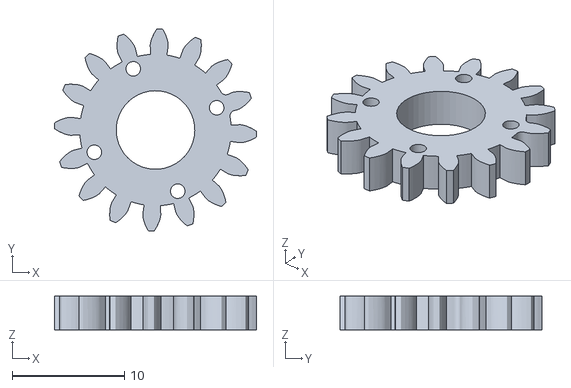
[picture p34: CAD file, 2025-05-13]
stls/head_1_driving_gear_1_body.stl
18.0 x 18.0 x 3.00

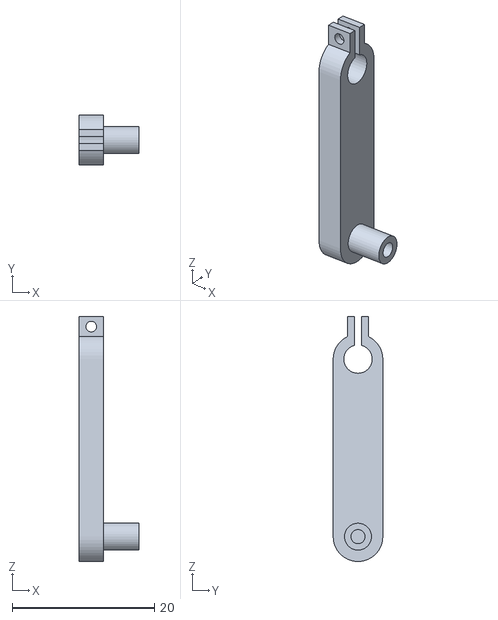
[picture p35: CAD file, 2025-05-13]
stls/arms_1_cranks_1_arm_servo_crank_r.stl
8.50 x 7.00 x 34.5

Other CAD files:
stls/drive_train_1_mount_r_i_1_body.stl
stls/drive_train_1_mount_l_o_1_body.stl
stls/drive_train_1_axles_1_r.stl
stls/arms_1_clamps_1_r.stl
stls/arms_1_cranks_1_arm_servo_crank_l.stl
stls/walle_3.0.f3d

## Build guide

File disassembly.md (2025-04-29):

# Disassembly

First things first. Let's take it apart. It's rather straight-forward with one caveat, which is the two hidden screws on the drive wheels. It also has a few non-standard screws but workarounds are available.

Remove 4 screws on the bottom

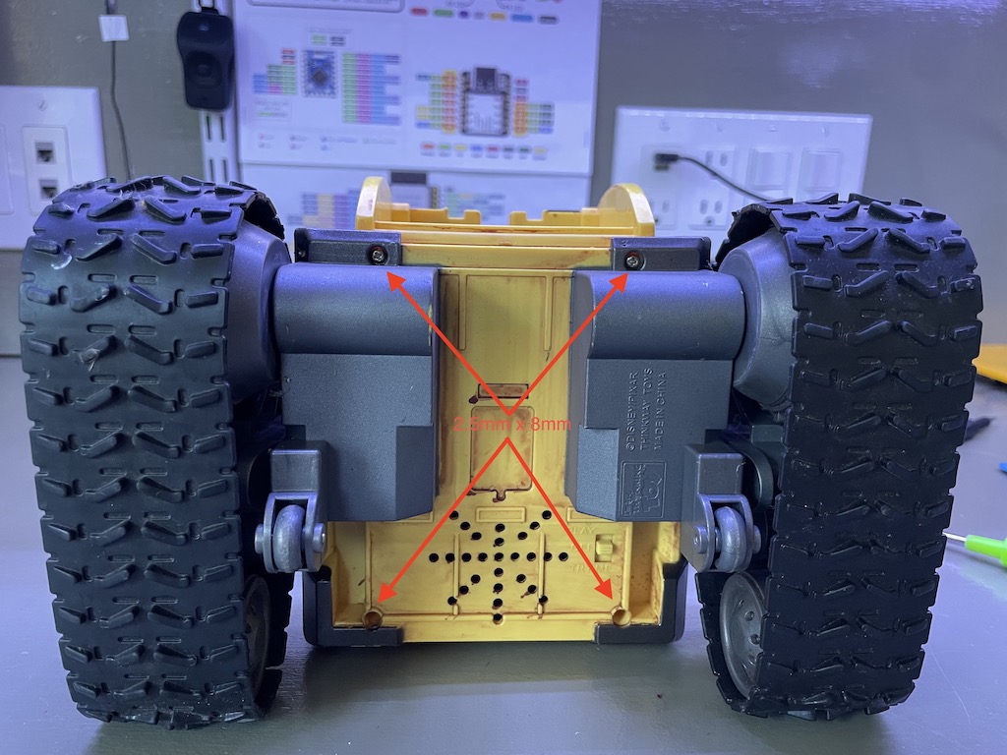
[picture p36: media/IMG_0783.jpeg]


Remove these 3 screws on the side of the tread assembly

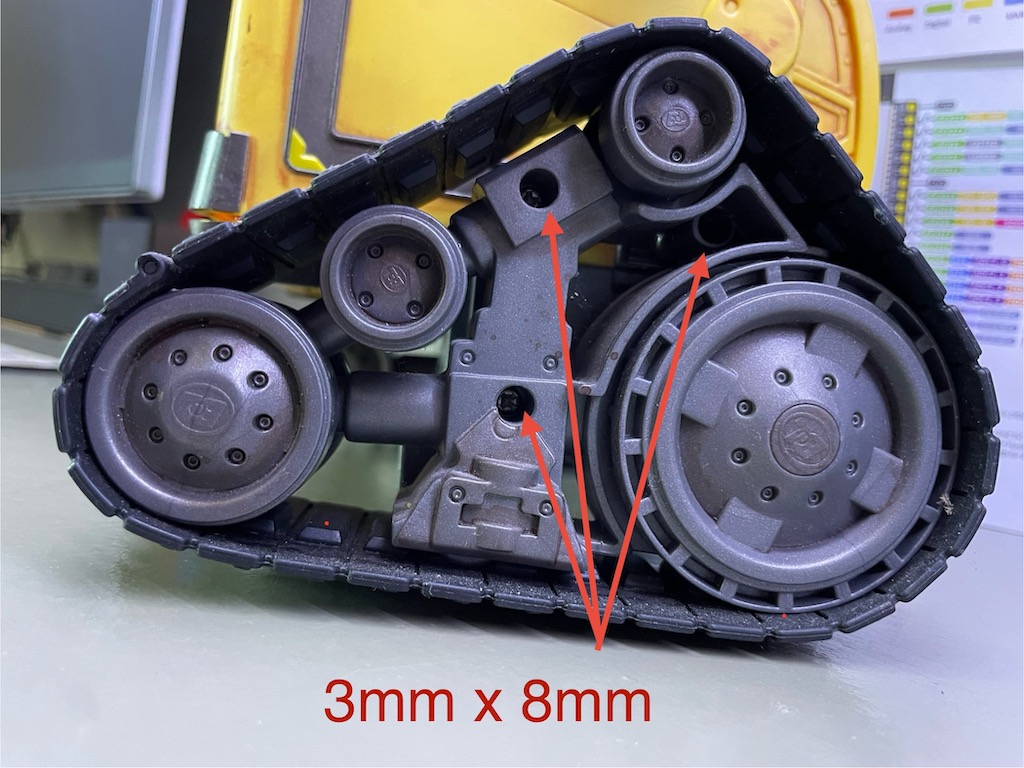
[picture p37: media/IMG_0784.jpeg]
tread screws


Drill a hole to expose the 4th screw

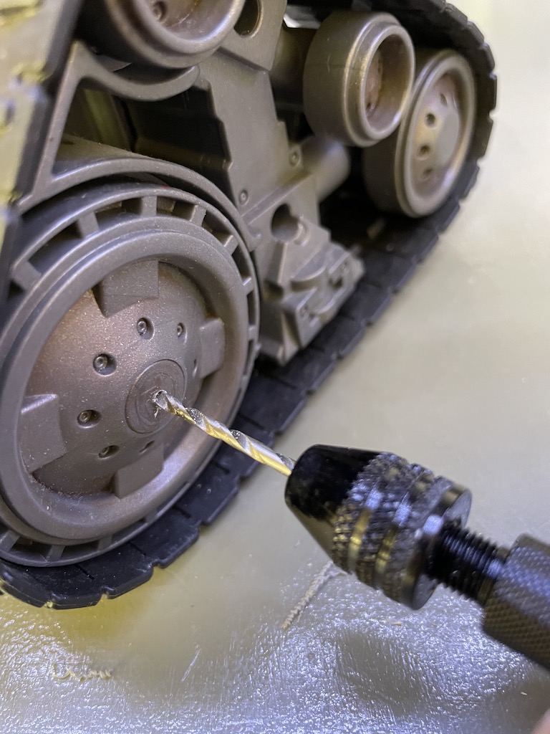
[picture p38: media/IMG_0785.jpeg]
drill


The tread assembly can now be removed.

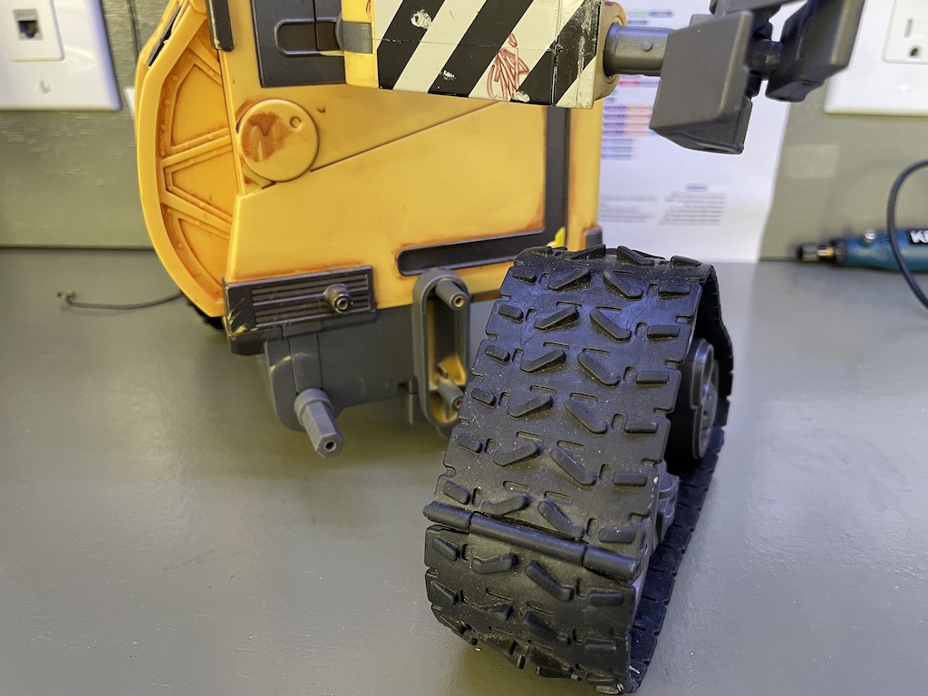
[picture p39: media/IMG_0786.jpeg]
removed


Repeat for the opposite side. The axle can be a little tight. Pull gently. Once both treads are removed, the bottom can be separated.

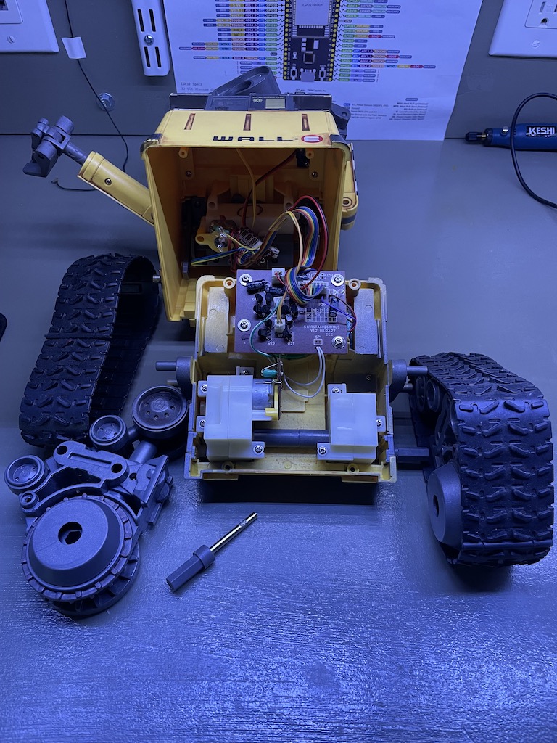
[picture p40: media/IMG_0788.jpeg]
separated


Now we can remove the main drivetrain and its control circuit. I am not planning to reuse any of this. But I am keeping the speaker and the switch.

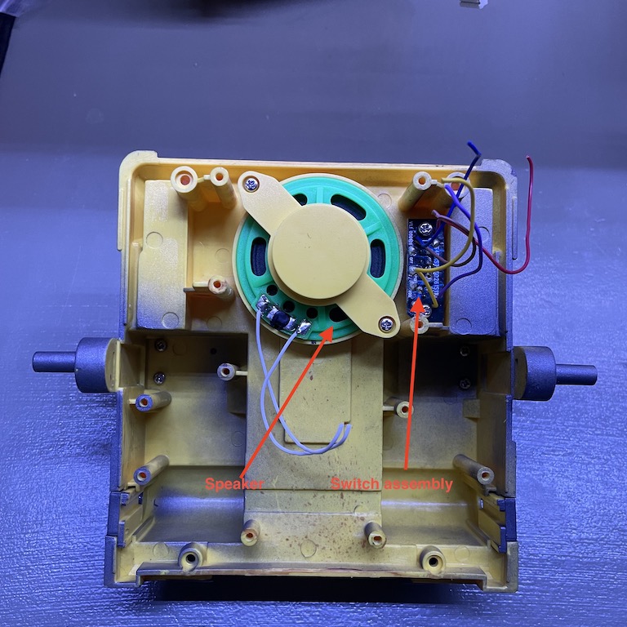
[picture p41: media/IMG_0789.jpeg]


Remove these 6 screws to separate the head and shoulder from the body.

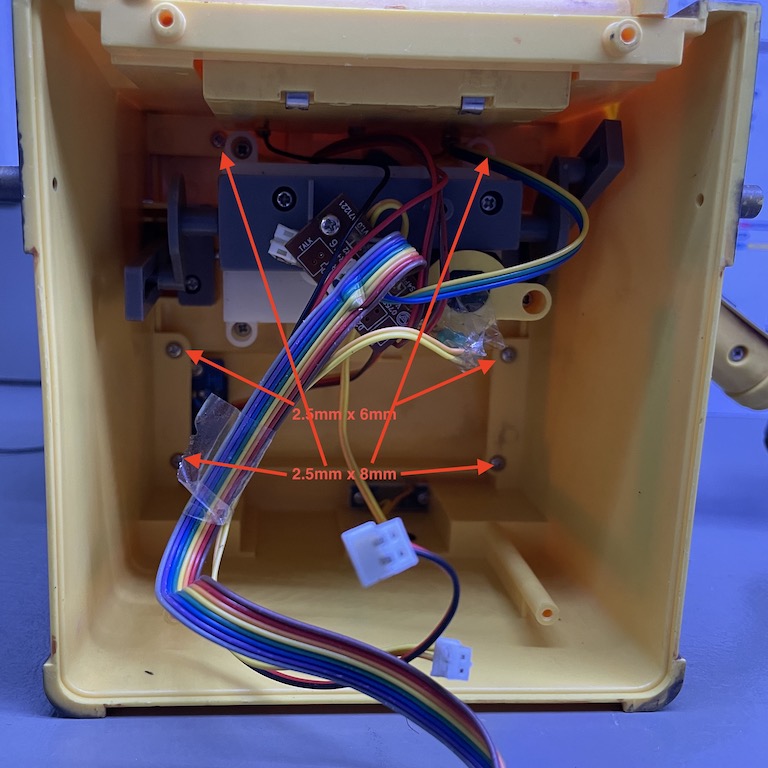
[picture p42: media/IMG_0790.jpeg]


Now, remove the screws fastening the drivetrain for the head and arms. The head assembly has four wires for the LEDs inside the eyes. There is an IR sensor for the remote on the shoulder.

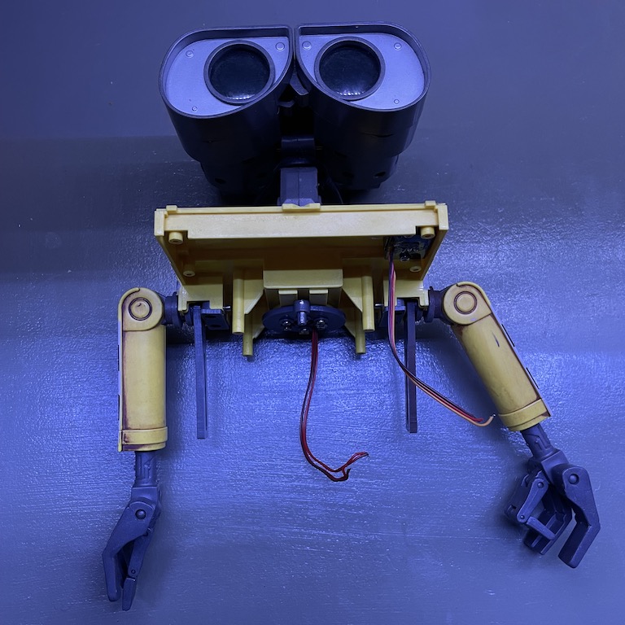
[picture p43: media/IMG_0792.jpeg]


To remove the head assembly from the shoulder, undo the following 6 screws.

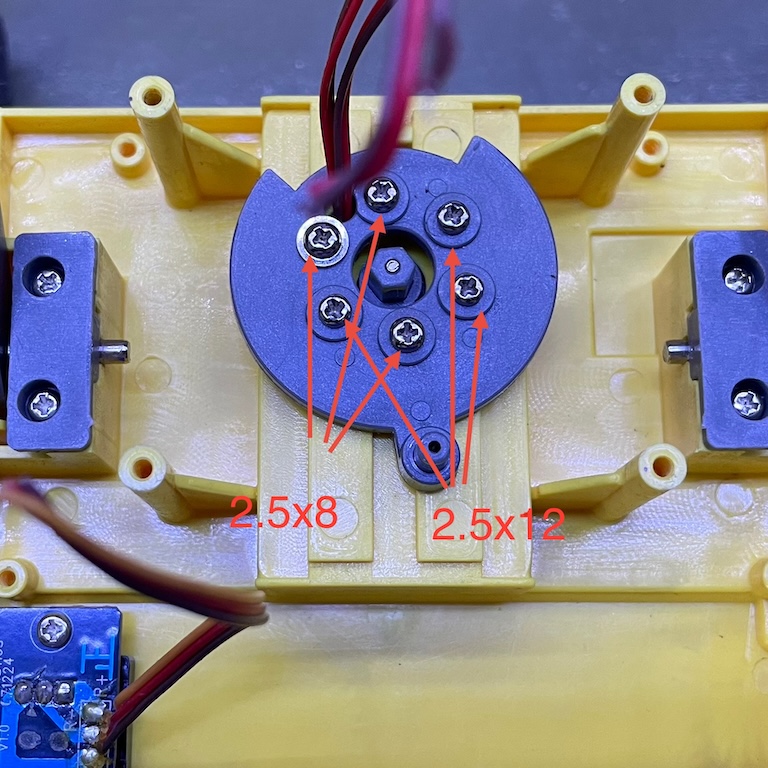
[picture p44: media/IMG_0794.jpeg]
shoulder


To remove battery compartment, first loosen the single screw to remove the back cover and expose four more screws.

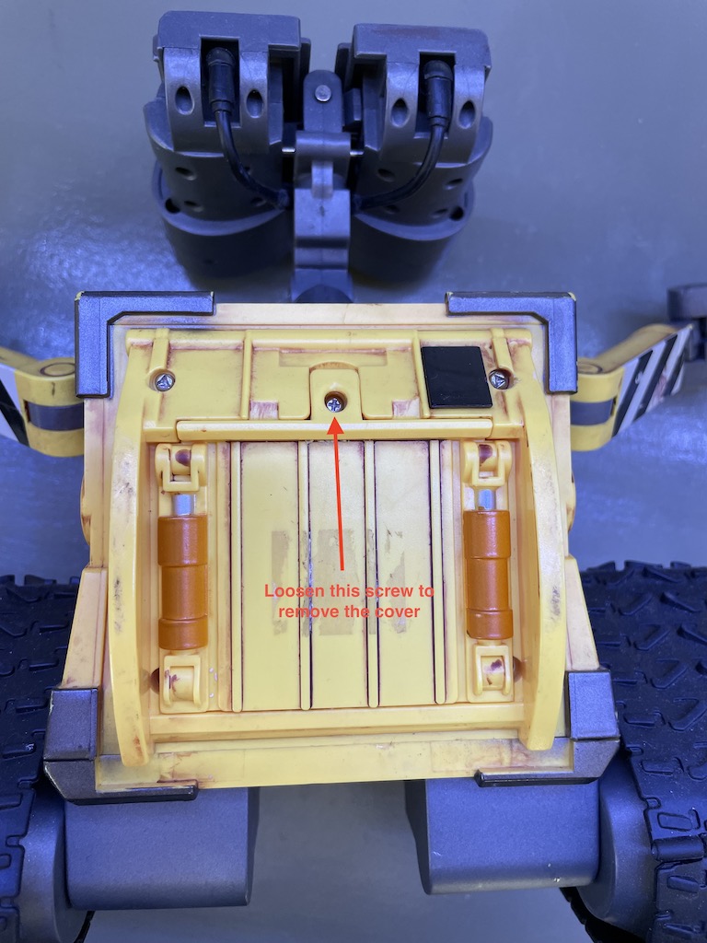
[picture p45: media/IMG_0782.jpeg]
cover


These four screws need a special triangle bit that I don't have. But a T7 Torx worked fine. I will replace them with normal 2.5x8 screws.

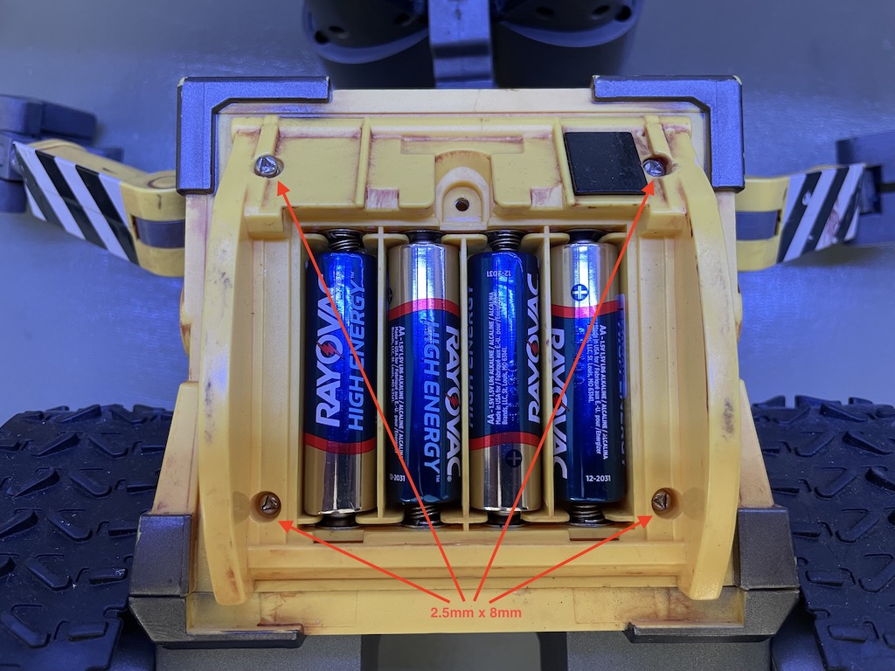
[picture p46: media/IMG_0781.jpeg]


The battery compartment contains the batteries as well as a second IR sensor for the remote control.

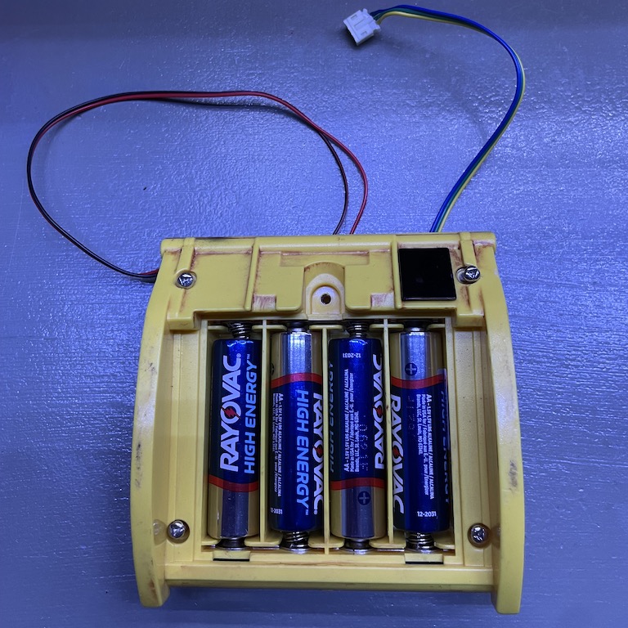
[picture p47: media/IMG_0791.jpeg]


Now the main components are separated. To recap, I am going to discard the following and keeping the rest.
* Main drivetrain for the treads.
* Drivetrain for the head and arms.
* Control circuits.

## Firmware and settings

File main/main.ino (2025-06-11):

#include <algorithm>
#include <array>
#include <queue>
#include <vector>

#include <Servo.h>

#include "src/DYPlayerArduino.h"
#define DECODE_NEC // Decodes NEC, NEC2, and ONKYO
#define DECODE_DISTANCE_WIDTH
#include "src/IRremote.hpp"

#ifdef NDEBUG
#define DEBUG_OUTPUT(...) Serial.print(__VA_ARGS__)
#else
#define DEBUG_OUTPUT(...)
#endif

#ifdef abs
#undef abs
#endif

template <typename T> T clamp(T v, T low, T high) {
  if (v < low) {
    return low;
  } else if (v > high) {
    return high;
  } else {
    return v;
  }
}

void resetIdleCount();

// Pin assignments
constexpr uint8_t pinIrRemote = 3;
constexpr uint8_t pinPushButton = 15;
constexpr uint8_t pinEyeTilter = 2;
constexpr uint8_t pinEyeLedL = 5;
constexpr uint8_t pinEyeLedR = 4;
constexpr uint8_t pinHead = 6;
constexpr uint8_t pinArmL = 7;
constexpr uint8_t pinArmR = 8;
constexpr uint8_t pinMotorLs = 14;
constexpr uint8_t pinMotorL1 = 12;
constexpr uint8_t pinMotorL2 = 13;
constexpr uint8_t pinMotorRs = 9;
constexpr uint8_t pinMotorR1 = 11;
constexpr uint8_t pinMotorR2 = 10;
constexpr uint8_t pinTrialMode = 26;
constexpr unsigned int millisIdle = 10000;
constexpr unsigned int millisBreathing = 3600;

// Servo limits, in terms of pulse width in microseconds
constexpr int minArmL = 2200;
constexpr int maxArmL = 450;
constexpr int minArmR = 700;
constexpr int maxArmR = 2450;
constexpr int minHead = 550;
constexpr int maxHead = 1950;

enum AnimationType {
  // Change the value linearly to a target value, over a specified duration, in
  // milliseconds
  LinearToOver,
  // Change the value linearly to a target value, at a specified speed, in
  // fraction per milliseconds
  LinearToAt,
  // Change the value linearly by an increment, over a specified duration
  LinearByOver,
  // Change the value linearly by an increment, at a specified speed
  LinearByAt,
  // Maintain the value for a specified duration
  Constant
};

struct Animation {
  AnimationType type;
  union {
    unsigned long millisDuration; // milliseconds
    float speed;                  // fraction per millisecond
  };
  float value; // target or incremental

  // to: absolute target value
  // by: incremental value
  // hold: maintain current value
  // over: duration in milliseconds
  // at: speed in fraction per millisecond
  // now: instantaneously

  static Animation toOver(float value, unsigned long duration) {
    return Animation{AnimationType::LinearToOver, {duration}, value};
  }

  static Animation toAt(float value, float speed) {
    return Animation{AnimationType::LinearToAt, {.speed = speed}, value};
  }

  static Animation byOver(float value, unsigned long duration) {
    return Animation{AnimationType::LinearByOver, {duration}, value};
  }

  static Animation byAt(float value, float speed) {
    return Animation{AnimationType::LinearByAt, {.speed = speed}, value};
  }

  static Animation toNow(float value) {
    return Animation{AnimationType::LinearToOver, {0L}, value};
  }

  static Animation byNow(float value) {
    return Animation{AnimationType::LinearByOver, {0L}, value};
  }

  static Animation holdOver(unsigned long duration) {
    return Animation{AnimationType::Constant, {duration}};
  }
};

class Animatable {
public:
  static void updateFrame() {
    unsigned long millisNow = millis();
    for (int i = 0; i < animatables.size(); i++) {
      animatables[i]->updateFrame(millisNow);
    }
  }

protected:
  static std::vector<Animatable *> animatables;

  float value_;
  std::queue<Animation> animationQueue;
  unsigned long millisStart = 0;
  float valueStart;

  Animatable() { animatables.push_back(this); }

  virtual void setValue(float value) { value_ = value; }
  float getValue() { return value_; }

public:
  void queueAnimation(Animation animation) {
    animationQueue.push(animation);
    if (animationQueue.size() == 1) {
      transitionToNextAnimation(millis());
    }
  }

  template <size_t N>
  void queueAnimations(const std::array<Animation, N> animations) {
    for (auto animation : animations) {
      queueAnimation(animation);
    }
  }

  bool isAnimating() { return !animationQueue.empty(); }

protected:
  void transitionToNextAnimation(unsigned long millisNow) {
    if (animationQueue.empty()) {
      millisStart = 0;
      return;
    }
    millisStart = millisNow;
    valueStart = value_;

    Animation &animation = animationQueue.front();
    if (animation.type == AnimationType::LinearByOver ||
        animation.type == AnimationType::LinearByAt) {
      // Calculate the target value based on the current value and the
      // increment.

      constexpr float epsilon = 0.05;
      float valueCurrent = getValue();

      float valueTarget = clamp(valueCurrent + animation.value, 0.0f, 1.0f);
      if (std::abs(valueCurrent - valueTarget) <= epsilon) {
        animationQueue.pop();
        transitionToNextAnimation(millisNow);
        return;
      }
      animation.value = valueTarget;
    }

    if (animation.type == AnimationType::LinearToAt ||
        animation.type == AnimationType::LinearByAt) {
      // Calculate the duration based on the speed and the increment.
      float valueCurrent = getValue();

      // animation.value is already target value, rather than the increment.
      unsigned long duration =
          std::abs(animation.value - valueCurrent) / animation.speed;

      animation.millisDuration = duration;
    }
  }

  void updateFrame(unsigned long millisNow) {
    if (animationQueue.empty()) {
      return;
    }

    resetIdleCount();

    Animation animation = animationQueue.front();
    switch (animation.type) {
    case AnimationType::LinearToOver:
    case AnimationType::LinearToAt:
    case AnimationType::LinearByOver:
    case AnimationType::LinearByAt: {
      // Target value and duration should've already been calculated.
      float fraction = static_cast<float>(millisNow - millisStart) /
                       static_cast<float>(animation.millisDuration);
      if (fraction >= 1.0) {
        setValue(animation.value);
        animationQueue.pop();
        transitionToNextAnimation(millisNow);
      } else {
        float valueNext =
            (1.0 - fraction) * valueStart + fraction * animation.value;
        setValue(valueNext);
      }

      break;
    }

    case AnimationType::Constant: {
      if (millisNow - millisStart >= animation.millisDuration) {
        animationQueue.pop();
        transitionToNextAnimation(millisNow);
      }
      break;
    }
    }
  }
};

std::vector<Animatable *> Animatable::animatables;

class AnimatableServo : public Animatable {
public:
  AnimatableServo(uint8_t pin, uint16_t min, uint16_t max)
      : pin_(pin), min_(min), max_(max), Animatable() {}

  void setValue(float value) override {
    Animatable::setValue(value);
    uint16_t us = static_cast<uint16_t>(value * static_cast<float>(max_) +
                                        (1 - value) * static_cast<float>(min_));
    // Specific to RP2040, since the Servo library uses PIO, attach() needs to
    // be called after setup() has begun. so we can't do it in the constructor.
    // For any other MCU, we can most likely move this to the constructor and
    // get rid of pin_
    if (!servo_.attached()) {
      if (max_ > min_) {
        servo_.attach(pin_, min_, max_);
      } else {
        servo_.attach(pin_, max_, min_);
      }
    }
    servo_.writeMicroseconds(us);
  }

private:
  Servo servo_;
  uint8_t pin_;
  uint16_t min_;
  uint16_t max_;
};

class Led : public Animatable {
public:
  Led(uint8_t pin) : pin_(pin), Animatable() { pinMode(pin, OUTPUT); }

  void setValue(float value) override {
    Animatable::setValue(value);
    analogWrite(pin_, static_cast<int>(value * 255.0));
  }

private:
  uint8_t pin_;
};

// Unidirectional motor, controlled by a PWM pin and a MOSFET
class UniMotor : public Animatable {
public:
  UniMotor(uint8_t pin) : pin_(pin), Animatable() { pinMode(pin, OUTPUT); }

  void setValue(float value) override {
    Animatable::setValue(value);
    analogWrite(pin_, static_cast<int>(value * 255.0));
  }

private:
  uint8_t pin_;
};

// Bidirectional motor, controlled by an H-bridge
class BiMotor : public Animatable {
  static constexpr float minValue = 0.20;

private:
  uint8_t pinSpeed_;
  uint8_t pin1_;
  uint8_t pin2_;

public:
  BiMotor(uint8_t pinSpeed, uint8_t pin1, uint8_t pin2)
      : pinSpeed_(pinSpeed), pin1_(pin1), pin2_(pin2), Animatable() {
    pinMode(pinSpeed, OUTPUT);
    pinMode(pin1, OUTPUT);
    pinMode(pin2, OUTPUT);
  }

  void setValue(float value) override {
    if (std::abs(value) <= minValue) {
      value = 0;
    }

    Animatable::setValue(value);

    if (value > 0) {
      digitalWrite(pin1_, 1);
      digitalWrite(pin2_, 0);
    } else if (value < 0) {
      digitalWrite(pin1_, 0);
      digitalWrite(pin2_, 1);
    } else {
      digitalWrite(pin1_, 0);
      digitalWrite(pin2_, 0);
    }
    analogWrite(pinSpeed_, static_cast<int>(std::abs(value) * 255.0));
  }
};

class PushButton {
  static constexpr int debounceThreshold = 100;

public:
  PushButton(int pin) : pin_(pin) {}

  void begin() {
    pinMode(pin_, INPUT_PULLUP);
    last_ = millis();
  }

  bool isPushed() {
    unsigned long now = millis();
    if (now - last_ < debounceThreshold) {
      return false;
    }
    last_ = now;
    int bitmap = digitalRead(pin_);
    // No hold and repeat. The button is only considered pushed
    // if it was released in the previous scan.
    if (bitmap == LOW && released_) {
      released_ = false;
      return true;
    }
    if (bitmap == HIGH) {
      released_ = true;
    }
    return false;
  }

private:
  int pin_;
  unsigned long last_ = 0;
  bool released_ = true;
};

class AudioQueue {
public:
  struct Entry {
    enum { Delay, Play } tag;
    unsigned long millisStart = 0;
    union {
      unsigned long duration;
      unsigned int index;
    };
  };

  static AudioQueue audioQueue;
  static void updateFrame() {
    unsigned long millisNow = millis();
    audioQueue.updateFrame(millisNow);
  }

  static void queueDelay(unsigned long duration) {
    Entry entry{
        .tag = Entry::Delay, .millisStart = millis(), duration = duration};
    audioQueue.queue.push(entry);
  }

  static void queuePlay(unsigned int index) {
    Entry entry{.tag = Entry::Play, .millisStart = millis(), index = index};
    audioQueue.queue.push(entry);
  }

  AudioQueue(DY::Player &player) : player_(player) {}

private:
  void updateFrame(unsigned long millisNow) {
    if (queue.empty()) {
      return;
    }

    resetIdleCount();

    Entry entry = queue.front();
    switch (entry.tag) {
    case Entry::Delay:
      if (millisNow > entry.millisStart + entry.duration) {
        queue.pop();
      }
      break;
    case Entry::Play:
      player_.playSpecified(entry.index);
      queue.pop();
      break;
    }
  }

protected:
  static std::queue<Entry> queue;
  DY::Player &player_;
};

std::queue<AudioQueue::Entry> AudioQueue::queue;

AnimatableServo head(pinHead, minHead, maxHead);
AnimatableServo leftArm(pinArmL, minArmL, maxArmL);
AnimatableServo rightArm(pinArmR, minArmR, maxArmR);
UniMotor eyeTilter(pinEyeTilter);
BiMotor leftTread(pinMotorLs, pinMotorL1, pinMotorL2);
BiMotor rightTread(pinMotorRs, pinMotorR1, pinMotorR2);
Led leftEye(pinEyeLedL);
Led rightEye(pinEyeLedR);
PushButton pushButton(pinPushButton);

DY::Player audioPlayer(&Serial1);
AudioQueue AudioQueue::audioQueue(audioPlayer);

unsigned long millisIdleStart;
float breathingPhase = 1; // a value in the range of [0-1]
boolean trialMode = false;

void resetIdleCount() {
  if (isIdling()) {
    breathingPhase = 1;
  }

  millisIdleStart = millis();
}

void setIdle() { millisIdleStart = 0; }

bool isIdling() { return millis() - millisIdleStart >= millisIdle; }

void demo() {
  // Hold, look left, right, then straight
  std::array<Animation, 5> headAnimation = {
      Animation::toAt(0.5, 0.0005), Animation::holdOver(500),
      Animation::toOver(0, 1000), Animation::toOver(1, 2000),
      Animation::toOver(0.5, 1000)};
  head.queueAnimations(headAnimation);

  // Hold, then blink twice
  std::array<Animation, 9> eyeAnimation = {
      Animation::toNow(1),      Animation::holdOver(4500),
      Animation::toOver(0, 20), Animation::holdOver(100),
      Animation::toOver(1, 20), Animation::holdOver(300),
      Animation::toOver(0, 20), Animation::holdOver(100),
      Animation::toOver(1, 20)};
  leftEye.queueAnimations(eyeAnimation);
  rightEye.queueAnimations(eyeAnimation);

  // Wait, then play wall-e sound
  AudioQueue::queueDelay(5000);
  AudioQueue::queuePlay(1);
}

void playNextAudio() {
  constexpr int audioFileCount = 10;
  static int index = 2;
  index++;
  if (index > audioFileCount) {
    index = 1;
  }
  AudioQueue::queueDelay(100);
  AudioQueue::queuePlay(index);
}

void stop() {
  std::array<Animation, 1> animations = {Animation::toOver(0, 400)};
  leftTread.queueAnimations(animations);
  rightTread.queueAnimations(animations);
}

void spinLeft() {
  leftTread.queueAnimation(Animation::toOver(-1, 200));
  rightTread.queueAnimation(Animation::toOver(1, 200));
}

void spinRight() {
  leftTread.queueAnimation(Animation::toOver(1, 200));
  rightTread.queueAnimation(Animation::toOver(-1, 200));
}

void forward() {
  leftTread.queueAnimation(Animation::toOver(1, 200));
  rightTread.queueAnimation(Animation::toOver(1, 200));
}

void backward() {
  leftTread.queueAnimation(Animation::toOver(-1, 200));
  rightTread.queueAnimation(Animation::toOver(-1, 200));
}

void forwardLeft() {
  leftTread.queueAnimation(Animation::toOver(0, 200));
  rightTread.queueAnimation(Animation::toOver(1, 200));
}

void forwardRight() {
  leftTread.queueAnimation(Animation::toOver(1, 200));
  rightTread.queueAnimation(Animation::toOver(0, 200));
}

void backwardLeft() {
  leftTread.queueAnimation(Animation::toOver(0, 200));
  rightTread.queueAnimation(Animation::toOver(-1, 200));
}

void backwardRight() {
  leftTread.queueAnimation(Animation::toOver(-1, 200));
  rightTread.queueAnimation(Animation::toOver(0, 200));
}

void leftArmUp() { leftArm.queueAnimation(Animation::toAt(1, 0.001f)); }

void leftArmDown() { leftArm.queueAnimation(Animation::toAt(0, 0.001f)); }

void rightArmUp() { rightArm.queueAnimation(Animation::toAt(1, 0.001f)); }

void rightArmDown() { rightArm.queueAnimation(Animation::toAt(0, 0.001f)); }

void leftArmMove(float value) {
  leftArm.queueAnimation(Animation::byAt(value, 0.001f));
}
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
void loop() {
  Animatable::updateFrame();
  AudioQueue::updateFrame();

  if (pushButton.isPushed()) {
    resetIdleCount();
    demo();
    return;
  }

  if (IrReceiver.decode()) {
    resetIdleCount();

    uint64_t code = IrReceiver.decodedIRData.decodedRawData;
    decode_type_t protocol = IrReceiver.decodedIRData.protocol;

    IrReceiver.resume();
    // The Roku remote control
    if (protocol == NEC) {
      switch (code) {
      case 3893872618: // Power
        demo();
        break;
      case 2573649898: // Back
        dance();
        break;
      case 4228106218: // Home
        homePosition();
        break;

      case 3860449258: // Up
        forward();
        break;
      case 3425945578: // Down
        backward();
        break;
      case 3776890858: // Left
        spinLeft();
        break;
      case 3526215658: // Right
        spinRight();
        break;
      case 3576350698: // OK
        stop();
        break;

      case 2272839658: // Repeat
        blinkTwice();
        break;
      case 2640496618: // Sleep
        tiltEye();
        break;
      case 2657208298: // Star
        breathe();
        break;

      case 3409233898: // Rewind
        lookLeft();
        break;
      case 3008153578: // Play/Pause
        playNextAudio();
        break;
      case 2857748458: // F. Fwd
        lookRight();
        break;

      case 2907883498: // Netflix
        forwardLeft();
        break;
      case 2991441898: // Hulu
        backwardLeft();
        break;
      case 3024865258: // AmazonPrime
        forwardRight();
        break;
      case 4077701098: // Disney
        backwardRight();
        break;

      case 4144547818: // Vudu
        leftArmUp();
        break;
      case 2974730218: // HBO
        leftArmDown();
        break;
      case 2841036778: // YouTube
        rightArmUp();
        break;
      case 4177971178: // Sling
        rightArmDown();
        break;

      case 4027566058: // Vol Up
        AudioQueue::queuePlay(2);
        break;
      case 4010854378: // Vol Down
        AudioQueue::queuePlay(3);
        break;
      case 3743467498: // Mute
        AudioQueue::queuePlay(1);
        break;
      }
    }

    // Custom remote control
    if (protocol == PULSE_DISTANCE) {
      byte *p = (byte *)(&code);
      byte correction = 0;
      for (int i = 0; i < 6; i++) {
        correction ^= p[i];
      }
      if (correction == 0) {
        static uint64_t prevCode = 0x000000008888; // The neutral state

        int8_t x1, y1;
        int8_t x2, y2;
        decodeJoystick(p[0], x1, y1);
        decodeJoystick(p[1], x2, y2);

        // if any of the button bits (16 - 40) has changed
        if ((code ^ prevCode) & 0xFFFFFF0000) {
          for (int i = 16; i < 40; i++) {
            bool curr = (code >> i) & 1;
            bool prev = (prevCode >> i) & 1;

            if (curr && !prev) {
              // Button pressed
              switch (i - 16) {
              case 0: // R1
                rightArmMove(0.1);
                break;
              case 1: // R2
                rightArmMove(-0.1);
                break;
              case 2: // L1
                leftArmMove(0.1);
                break;
              case 3: // L2
                leftArmMove(-0.1);
                break;
              case 4: // SEL
                wink();
                break;
              case 5: // MODE
                demo();
                break;
              case 6: // N/A
                break;
              case 7: // START
                playNextAudio();
                break;
              case 8: // A
                backward();
                break;
              case 9: // X
                spinLeft();
                break;
              case 10: // B
                spinRight();
                break;
              case 11: // Y
                forward();
                break;
              case 12: // Down
                tiltEye();
                break;
              case 13: // Up
                homePosition();
                break;
              case 14: // Right
                rotateHeadBy(0.1);
                break;
              case 15: // Left
                rotateHeadBy(-0.1);
                break;
              case 16: // Joystick1
                stop();
                break;
              case 17: // Joystick2
                dance();
                break;
              default:
                break;
              }
            }
          }
        }

        // Joystick 1 position changed
        if ((code ^ prevCode) & 0x00000000FF) {
          // Normalize x and y values. Range: [-1,1]
          float xNormalized = x1 / 7.0;
          float yNormalized = y1 / 7.0;

          float xSign = xNormalized >= 0 ? 1 : -1;
          float ySign = yNormalized >= 0 ? 1 : -1;

          float left, right;
          if (xSign == ySign) {
            left = ySign * max(abs(xNormalized), abs(yNormalized));
            right = ySign * (abs(yNormalized) - abs(xNormalized));
          } else {
            right = ySign * max(abs(xNormalized), abs(yNormalized));
            left = ySign * (abs(yNormalized) - abs(xNormalized));
          }
          leftTread.setValue(left);
          rightTread.setValue(right);
        }

        // Joystick 2 is not in the neutral position
        if (y2 != 0) {
          static unsigned long last = millis();

          // Range with which a normalized x value is considered
          // "centered"
          const float thresholdLeft = -0.5;
          const float thresholdRight = 0.5;

          // Normalize x and y values. Range: [-1,1]
          float xNormalized = x2 / 7.0;
          float yNormalized = y2 / 7.0;

          bool moveLeft = xNormalized <= thresholdRight;
          bool moveRight = xNormalized >= thresholdLeft;

          // Calculate the speed to move: fast, slow, or still
          float ySign = yNormalized >= 0 ? 1 : -1;
          float yAbsolute = abs(yNormalized);
          float speed;
          if (yAbsolute > 0.85) {
            speed = 0.0003;
          } else if (yAbsolute > 0.25) {
            speed = 0.00015;
          } else {
            speed = 0;
          }

          // Only queue an animation if the queue is empty. Otherwise
          // it'd be animating long after the joystick is returned to
          // the neutral position, which is not what we want.
          if (moveLeft && speed != 0 && !leftArm.isAnimating()) {
            leftArm.queueAnimation(Animation::byAt(0.1 * ySign, speed));
          }

          if (moveRight && speed != 0 && !rightArm.isAnimating()) {
            rightArm.queueAnimation(Animation::byAt(0.1 * ySign, speed));
          }
        }

        prevCode = code;
      } else {
        DEBUG_OUTPUT("Error detected\n");
      }
    }
  }

  if (isIdling()) {
    leftTread.setValue(0);
    rightTread.setValue(0);

    unsigned long idleDuration = (millis() - millisIdleStart) % millisBreathing;

    if (idleDuration < millisBreathing / 2.0) {
      breathingPhase = 1.0 - idleDuration / (millisBreathing / 2.0);
    } else {
      breathingPhase = -1.0 + idleDuration / (millisBreathing / 2.0);
    }

    leftEye.setValue(breathingPhase);
    rightEye.setValue(breathingPhase);
  }
}

void decodeJoystick(byte code, int8_t &x, int8_t &y) {
  if (code & 0x08) {
    x = -(code & 0x07);
  } else {
    x = code & 0x07;
  }

  if (code & 0x80) {
    y = -((code & 0x70) >> 4);
  } else {
    y = (code & 0x70) >> 4;
  }
}

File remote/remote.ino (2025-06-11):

#define FEEDBACK_LED_IS_ACTIVE_LOW
#define DECODE_NEC
#include "src/IRremote.hpp"

#define NDEBUG
// #undef NDEBUG

#ifdef NDEBUG
#define DEBUG_OUTPUT(...) Serial.print(__VA_ARGS__)
#else
#define DEBUG_OUTPUT(...)
#endif

class KeyMatrix {
private:
  int rows_, cols_;
  uint8_t *pinsRows_, *pinsCols_;
  byte *bitmap;

public:
  // No memory management for row and col pin arrays. Pass arrays on the heap.
  KeyMatrix(int rows, int cols, uint8_t *pinsRows, uint8_t *pinsCols)
      : rows_(rows), cols_(cols), pinsRows_(pinsRows), pinsCols_(pinsCols) {
    // (cols+1)>>3 == ceiling(cols/8)
    bitmap = (byte *)malloc(rows * ((cols + 1) >> 3));
  }

  void begin() {
    for (int c = 0; c < cols_; c++) {
      pinMode(pinsCols_[c], OUTPUT);
      digitalWrite(pinsCols_[c], HIGH);
    }
    for (int r = 0; r < rows_; r++) {
      pinMode(pinsRows_[r], INPUT_PULLUP);
    }
  }

  byte *read() {
    for (int c = 0; c < cols_; c++) {
      digitalWrite(pinsCols_[c], LOW);
      for (int r = 0; r < rows_; r++) {
        set(r, c, !digitalRead(pinsRows_[r]));
      }
      digitalWrite(pinsCols_[c], HIGH);
    }
    return bitmap;
  }

private:
  inline void set(int row, int col, bool value) {
    byte *target = &bitmap[(row * cols_ + col) >> 3];
    int bit = col & 0x07;
    if (value) {
      *target |= 1 << bit;
    } else {
      *target &= ~(1 << bit);
    }
  }
};

class PushButton {
private:
  int pin_;

public:
  PushButton(int pin) : pin_(pin) {}

  void begin() { pinMode(pin_, INPUT_PULLUP); }

  inline bool read() { return !digitalRead(pin_); }
};

class Joystick {
private:
  int pinHigh_;
  int pinX_;
  int pinY_;

public:
  Joystick(int pinHigh, int pinX, int pinY)
      : pinHigh_(pinHigh), pinX_(pinX), pinY_(pinY) {}

  void begin() {
    pinMode(pinHigh_, OUTPUT);
    pinMode(pinX_, INPUT);
    pinMode(pinY_, INPUT);

    digitalWrite(pinHigh_, HIGH);
    digitalWrite(pinHigh_, LOW);
  }

  byte read() {
    digitalWrite(pinHigh_, HIGH);
    float x = round(analogRead(pinX_) * (7.0 / 512.0) - 7.0);
    float y = round(7.0 - analogRead(pinY_) * (7.0 / 512.0));

    // IrSender doesn't like it when all bits are zero. So we use the
    // non-canonical representation of 0 b1000 to avoid all zero bits
    digitalWrite(pinHigh_, LOW);
    byte result = 0;
    result |= x <= 0 ? 0x08 : 0x00;
    result |= (uint8_t)(abs(x));
    result |= y <= 0 ? 0x80 : 0x00;
    result |= (uint8_t)(abs(y)) << 4;
    return result;
  }
};

class IrRemote {
private:
  uint8_t pin_;

public:
  IrRemote(uint8_t pin) : pin_(pin) {}

  void begin() { IrSender.begin(pin_); }

  void send(byte *data, int len) {
#ifdef NDEBUG
    Serial.print("Sending");
    char buffer[8];
    for (int i = 0; i < len; i++) {
      sprintf(buffer, " %02X", data[i]);
      Serial.print(buffer);
    }
    Serial.println();
#endif

    IrSender.sendPulseDistanceWidthFromArray(&NECProtocolConstants,
                                             (IRRawDataType *)data, len * 8, 0);
  }
};

IrRemote remote(10);

Joystick joystick1(A5, A2, A3);
Joystick joystick2(A5, A6, A7);

PushButton directButtons[] = {PushButton(A0), PushButton(A1)};

constexpr int rows = 2;
constexpr int cols = 8;
uint8_t pinsRows[rows] = {11, 12};
uint8_t pinsCols[cols] = {2, 3, 4, 5, 6, 7, 8, 9};
KeyMatrix matrix(rows, cols, pinsRows, pinsCols);

void setup() {
#ifdef NDEBUG
  Serial.begin(115200);
#endif

  remote.begin();

  for (int i = 0; i < sizeof(directButtons) / sizeof(PushButton); i++) {
    directButtons[i].begin();
  }

  joystick1.begin();
  joystick2.begin();
  matrix.begin();
}

void loop() {
  static unsigned long last = millis();
  unsigned long now = millis();
  // IR receiver needs about 100 ms to receive and process a frame.
  if (now - last < 120) {
    return;
  }
  last = now;

  // Bytes 0-1: left and right joysticks
  // y3 y2 y1 y0 x3 x2 x1 x0
  // Bytes 2-3: matrix buttons
  // Byte 4: other buttons
  // Byte 5: xor of other bytes
  byte data[6];
  data[0] = joystick1.read();
  data[1] = joystick2.read();

  byte *b = matrix.read();
  data[2] = b[0];
  data[3] = b[1];

  data[4] = 0;
  for (int i = 0; i < sizeof(directButtons) / sizeof(PushButton); i++) {
    if (directButtons[i].read()) {
      data[4] |= 1 << i;
    } else {
      data[4] &= ~(1 << i);
    }
  }

  data[5] = data[0] ^ data[1] ^ data[2] ^ data[3] ^ data[4];

  // If the state hasn't been remaining neutral, we use an exponential
  // backoff strategy for resending the same neutral state.
  static unsigned long interval = 2;
  byte neutral = data[0] == 0x88 && data[1] == 0x88 && data[2] == 0 &&
                 data[3] == 0 && data[4] == 0;
  if (!neutral) {
    interval = 2;
    remote.send(data, sizeof(data) / sizeof(byte));
  } else {
    static unsigned long last = millis();
    if (now - last >= interval) {
      remote.send(data, sizeof(data) / sizeof(byte));
      last = now;
      interval = interval * 1.5;
    }
  }
}

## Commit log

2025-01-17 Servo utils
2025-01-17 Arm servo prototyping video
2025-01-17 Servo calibrate and sweep.
2025-01-20 Update arm servos
    [arm_servo_clamp.stl, arm_servo_crank.stl]
2025-01-20 Update arm servo crank
    [arm_servo_crank.stl]
2025-01-28 dy-sv17f prototype
2025-02-01 Monted PCB
2025-02-17 Servo calibration
2025-02-17 Bug fix - mismatched curly brackets
    [main.ino]
2025-02-18 Fix audio issue and add some documentation.
    [main.ino]
2025-02-18 Change demo audio track.
2025-03-27 Remove debug print
2025-04-05 Main: bug fixes, debugging, tuning, etc.
    [main.ino]
2025-04-05 Disable LED feedback for the transmitter
2025-04-29 Update schematics
2025-05-16 Pictures of dev boards
2025-05-16 Add breadbord wiring
2025-05-16 Some reorg
    [arms_clamps_arm_servo_clamp_l.stl, arms_clamps_arm_servo_clamp_r.stl, arms_cranks_arm_servo_crank_l.stl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]
2025-05-17 Update perfboard wiring
2025-05-19 Update wiring
2025-05-21 Update main schematic
2025-05-25 Change pins; Refactor; Bug fixes.
    [main.ino]
2025-05-26 Update doc and schematic
2025-05-28 Update drivetrain doc and debug sketch
2025-05-30 Update 3d models
    [arms_1_clamps_1_l.stl, arms_1_clamps_1_r.stl, arms_1_cranks_1_arm_servo_crank_l.stl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]
2025-05-30 3d model link
    [walle_3.0.f3d]
2025-06-03 Remote range; schematic diagram.
2025-06-05 Finalize button functions
2025-06-09 Fix pins for eyes
    [main.ino]
